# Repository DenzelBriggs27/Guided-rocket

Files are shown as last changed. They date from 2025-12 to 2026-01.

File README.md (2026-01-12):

# Guided-rocket
Project submission for an aerodynamically controlled rocket, with active stabilization achieved by aft fin control. The fins are controlled by a custom-made PCB based around the STM32f446RET6 MCU.
The goal of this rocket is to stabilize trajectory on the roll, pitch, and yaw, axes by deflecting the aft fins of the rocket, producing controlled side forces. This project will incorporate CFD, filters, and control systems to achieve this goal. 

This project is a step in my pursuit of a career in aerospace, granting me new knowledge in various areas that are difficult to gain hands-on experience with. This project could not be done without funding for the IC's.

CAD:

Screenshot 2025-12-11 at 12 46 26 PM

There were tons of updates and small changes made periodically, so I'm just going to show the finished product and do a general description of the process and mechanics.

Screenshot 2025-12-11 at 9 12 27 AM

This rocket is meant to fly on the 29mm G80t motor, which doesn't leave much room in the aft section for much, so I had to get creative with a servo linkage to the fins with a custom-made horn. The fins are connected to a connector which allows them to slot into a small circular bearing.

Screenshot 2025-12-11 at 12 00 54 PM
The servos are controlled by a pcb near the aft of the rocket

Screenshot 2025-12-11 at 12 01 56 PM
Screenshot 2025-12-11 at 12 03 56 PM

The parabay will hold the parachute and will separate after apogee, a raceway cable will travel along the side of the interior, containing the servos power and pwm wires.

Screenshot 2025-12-11 at 12 10 56 PM

Above the parabay is the lipo housing and avionics bay, the whole vehicle is powered by a 7.4v 2600mAh battery, supplying to the servos and flight computer. The avionics bay consists of my primary custom flight controller, a radio, and a microsd card breakout board for telemetry and flight data logging respectively.

Untitled design (3)

The ellipsoidal nose cone contains an esp32 s3 module with an ov2640 cam, this allows not only for footage, but for bluetooth and wifi capabilities, allowing setup processes such as fin actuation tests to be run from a phone.

PCB:

Screenshot 2025-12-12 at 4 37 38 PM
Screenshot 2025-12-12 at 4 47 43 PM

I designed a custom PCB for telemetry and guidance calculations, centered around a STM32f446RET6 MCU, and powered by a 7.4v LiPo battery. It has 3 IMUS: BMI088, H3LIS331DL, and a BNO085. These IMUs were chosen for their different G ranges, their data will be integrated into a Kalman filter, then used to calculate the correct fin deflection angle to correct the rocket's orientation. The board also has a SAM-M10q-00b GNSS receiver, a bmp390 altimeter, 2 pyro charges with continuity detection, 4 pwm outputs, an SPI output, and a UART output for telemetry with an XBee 900hp over the 900 mHz band. This radio link allows for commands to be sent by the ground center, for which I designed a slightly different PCB:

Screenshot 2025-12-11 at 1 38 38 PM
Screenshot 2025-12-11 at 1 39 33 PM
This PCB and a second xbee900hp allows for a radio datalink between the rocket and ground station, with a maximum range of ~28 miles. Over this radio datalink, telemetry (orientation, position, velocity, acceleration) and commands (fin tests, flight presets) will be sent.

Thanks for viewing my project!

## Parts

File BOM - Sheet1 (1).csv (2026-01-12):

Item | cost | total
all ics | 126.87 | 171.87
pcb order | 45

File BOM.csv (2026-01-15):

PCBWay Bom Quotation, Product No.:T-3P2W1045433A
Item # | *Designator | *Qty | *Mfg Part # | Vendor Part # | *Package/Footprint | *Unit Price(2 sets) | *Total | *Delivery Time | *Actual Purchase Mfg Part # | *PCBWay Note | Customer Reply | PCBWay Update
1 | C1, C10, C2, C3, C4, C5 | 6 | 100n |  | 0402 | $0.004 | $0.048 |  | CC0402KRX7R6BB104
2 | C11, C12 | 2 | 10p |  | 0402 | $0.007 | $0.028 |  | TCC0402COG100J500AT
3 | C13, C6 | 2 | 10u |  | 0603 | $0.048 | $0.192 |  | 0603X106M100NT
4 | C14 | 1 | 22u |  | 0805 | $0.162 | $0.324 |  | GRM21BR60J226ME39L
5 | C15, C16, C17, C18, C19, C21, C22, C25 | 8 | 0.1uf |  | 0402 | $0.003 | $0.048 |  | 0402B104K250NT
6 | C20, C26, C28 | 3 | 10uf |  | 0603 | $0.036 | $0.216 |  | 0603X106M100NT
7 | C23, C24 | 2 | 22pF |  | 0402 | $0.010 | $0.040 |  | CC0402JRNPO7BN220
8 | C27, C29, C38 | 3 | 22uF |  | 0805 | $0.065 | $0.390 |  | GRM21BR60J226ME39L
9 | C37 | 1 | 2.2uf |  | 0603 | $0.077 | $0.154 |  | TCC0603X5R225K100CT
10 | C41, C42 | 2 | 0.1u |  | 0402 | $0.010 | $0.040 |  | CC0402KRX7R6BB104
11 | C43 | 1 | 4.7u |  | 0402 | $0.065 | $0.130 |  | 0402X475M6R3NT
12 | C7 | 1 | 10n |  | 0402 | $0.016 | $0.032 |  | 0402B103K500NT
13 | C8, C9 | 2 | 1u |  | 0402 | $0.015 | $0.060 |  | 0402X105K100NT
14 | D1, D2 | 2 | RED |  | 0201 | $0.180 | $0.720 |  | XL-0201SURC | XL-0201SURC
15 | D3 | 1 | LTST-S270GKT |  | LTST_S270GKT | $0.116 | $0.232
16 | FB1 | 1 | FerriteBead |  | 0603 |  |  |  |  | Sunlord GZ1608D121TF
17 | J1 | 1 | 39357-0004 |  | 393570004 | $3.018 | $6.036
18 | J10, J5 | 2 | 1769 |  | 1769 | $1.173 | $4.692 |  |  | Adafruit Industries LLC
19 | J2 | 1 | Conn_01x04_Pin |  | PinHeader_1x04_P2.54mm_Vertical | $0.322 | $0.644 |  | B-2100S04P-A110 | B-2100S04P-A110
20 | J4, J7 | 2 | 1985849 |  | PHOENIX_1985849 | $1.454 | $5.816
21 | J6 | 1 | 1050171001 |  | MOLEX_1050171001 | $0.841 | $1.682
22 | J8, J9 | 2 | PRT-16766 |  | CONN_BM04B-SRSS-TB_SPK | $1.173 | $4.692 |  |  | PRT-16766
23 | L1, L2 | 2 | 22uH |  | 0603 | $0.066 | $0.264 |  | CMI160808J220KT | CMI160808J220KT brand FH
24 | L4 | 1 | 10uH |  | 0603 | $0.458 | $0.916 |  | SCL1608S100KSP | W SCL1608S100KSP brand Sunltech.
25 | LS1 | 1 | CMI-9653S-SMT |  | CUI_CMI-9653S-SMT | $5.019 | $10.038 |  | CMI-9653S-SMT-TR | CMI-9653S-SMT-TR
26 | R1, R10, R11 | 3 | 10k |  | 0402 | $0.004 | $0.024 |  | RC0402FR-0710KL
27 | R12, R5, R9 | 3 | 100 |  | 0402 | $0.004 | $0.024 |  | RC0402FR-07100RL
28 | R13, R14, R8 | 3 | 150 |  | 0402 | $0.004 | $0.024 |  | 0402WGF1500TCE
29 | R15 | 1 | 400 |  | 0805 | $0.833 | $1.666 |  | TR0805B400RP0525Z
30 | R16, R17 | 2 | 4.7k |  | 0402 | $0.005 | $0.020 |  | 0402WGF4701TCE
31 | R2, R7 | 2 | 1k |  | 0402 | $0.006 | $0.024 |  | RC0402FR-071KL
32 | R21, R4 | 2 | 470K |  | 0603 | $0.010 | $0.040 |  | RC0603FR-07470KL
33 | R22 | 1 | 150K |  | 0603 | $0.017 | $0.034 |  | 0603WAF1503T5E
34 | R3 | 1 | 150K |  | 0402 | $0.010 | $0.020 |  | 0402WGF1503TCE
35 | R6 | 1 | 100k |  | 0402 | $0.008 | $0.016 |  | 0402WGF1003TCE
36 | S1, S2, S3 | 3 | 450404015514 |  | 450404015514 | $1.460 | $8.760
37 | U1 | 1 | BNO085 |  | IC_BNO085 | $15.094 | $15.094 | 1
38 | U11, U12 | 2 | IRLML6344TRPBF | IRLML6344TRPBF | IRLML6344TRPBF | $1.001 | $4.004
39 | U13 | 1 | USBLC6-2SC6 |  | USBLC6_2SC6 | $0.722 | $1.444
40 | U14 | 1 | TPS2113ADRBR |  | TPS2113ADRBR | $1.065 | $2.130
41 | U15, U5 | 2 | TPS62160QDSGRQ1 |  | DSG0008A | $0.545 | $2.180
42 | U2 | 1 | BMI088 |  | BMI088 | $5.251 | $10.502
43 | U3 | 1 | TPS62177DQCT |  | TPS62177DQCT | $0.781 | $1.562
44 | U4 | 1 | AMS1117-3.3 |  | SOT-223-3_TabPin2 | $0.559 | $1.118 |  |  | AMS SOT-223
45 | U6 | 1 | BMP390L |  | XDCR_BMP390L | $4.495 | $8.990
46 | U7 | 1 | ABX00083 |  | ABX00083 | $19.300 | $19.300 | 1
47 | U8 | 1 | STM32F446RET6 |  | LQFP-64_10x10mm_P0.5mm | $4.830 | $9.660
48 | U9 | 1 | H3LIS331DL |  | H3LIS331DL | $21.368 | $21.368 | 1
49 | Y1 | 1 | 16MHz crystal |  | Crystal_SMD_3225-4Pin_3.2x2.5mm |  |  |  |  | X322516MMB4SI
50 | Y2 | 1 | NX3215SA-32.768K-STD-MUA-8 |  | XTAL_NX3215SA-32.768K-STD-MUA-8 | $0.367 | $0.734
 |  |  |  |  |  | Component Cost | $146.17
 |  |  |  |  |  | Shipping Cost | $43.50
 |  |  |  |  |  | PCB Cost
 |  |  |  |  |  | V0 Member 0% off | $0.00
 |  |  |  |  |  | All Total 2 Sets | $189.67

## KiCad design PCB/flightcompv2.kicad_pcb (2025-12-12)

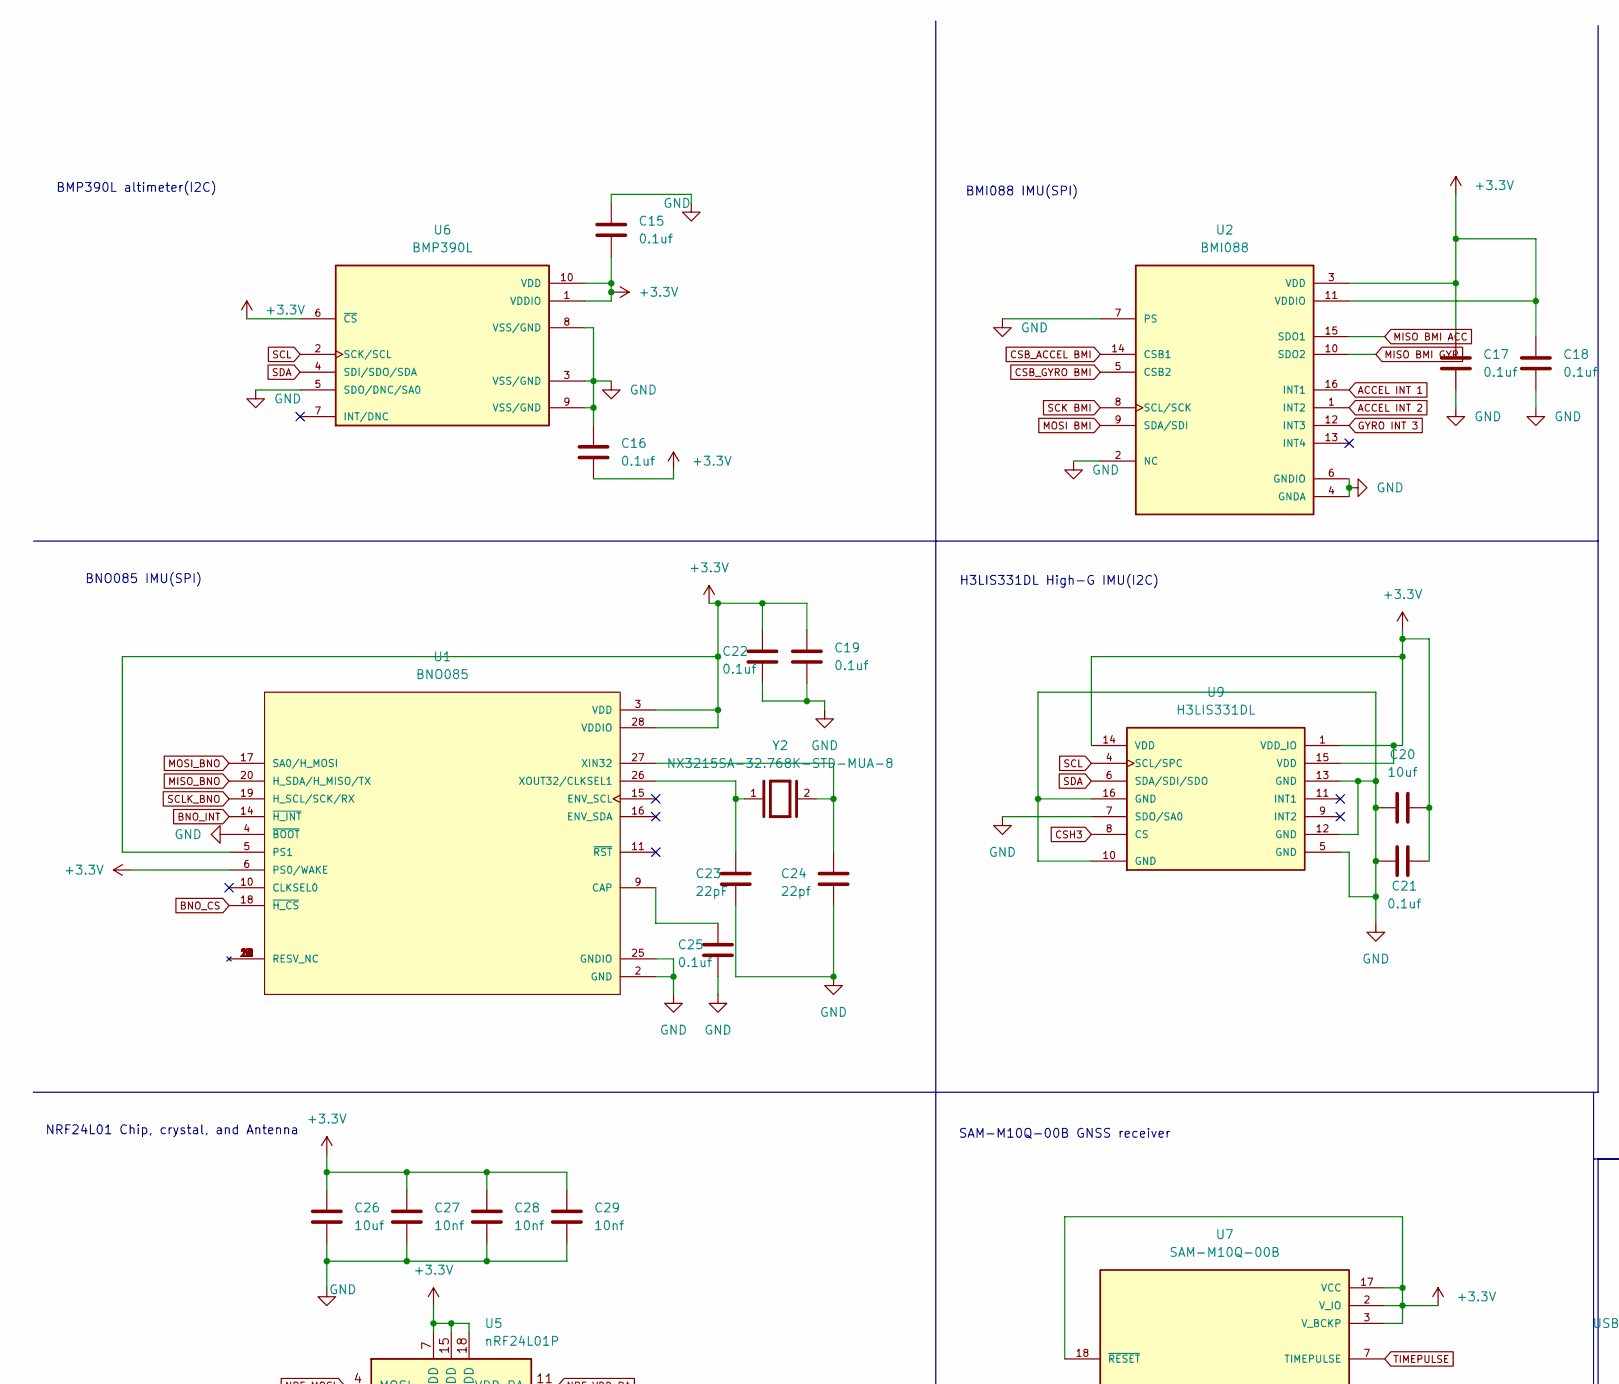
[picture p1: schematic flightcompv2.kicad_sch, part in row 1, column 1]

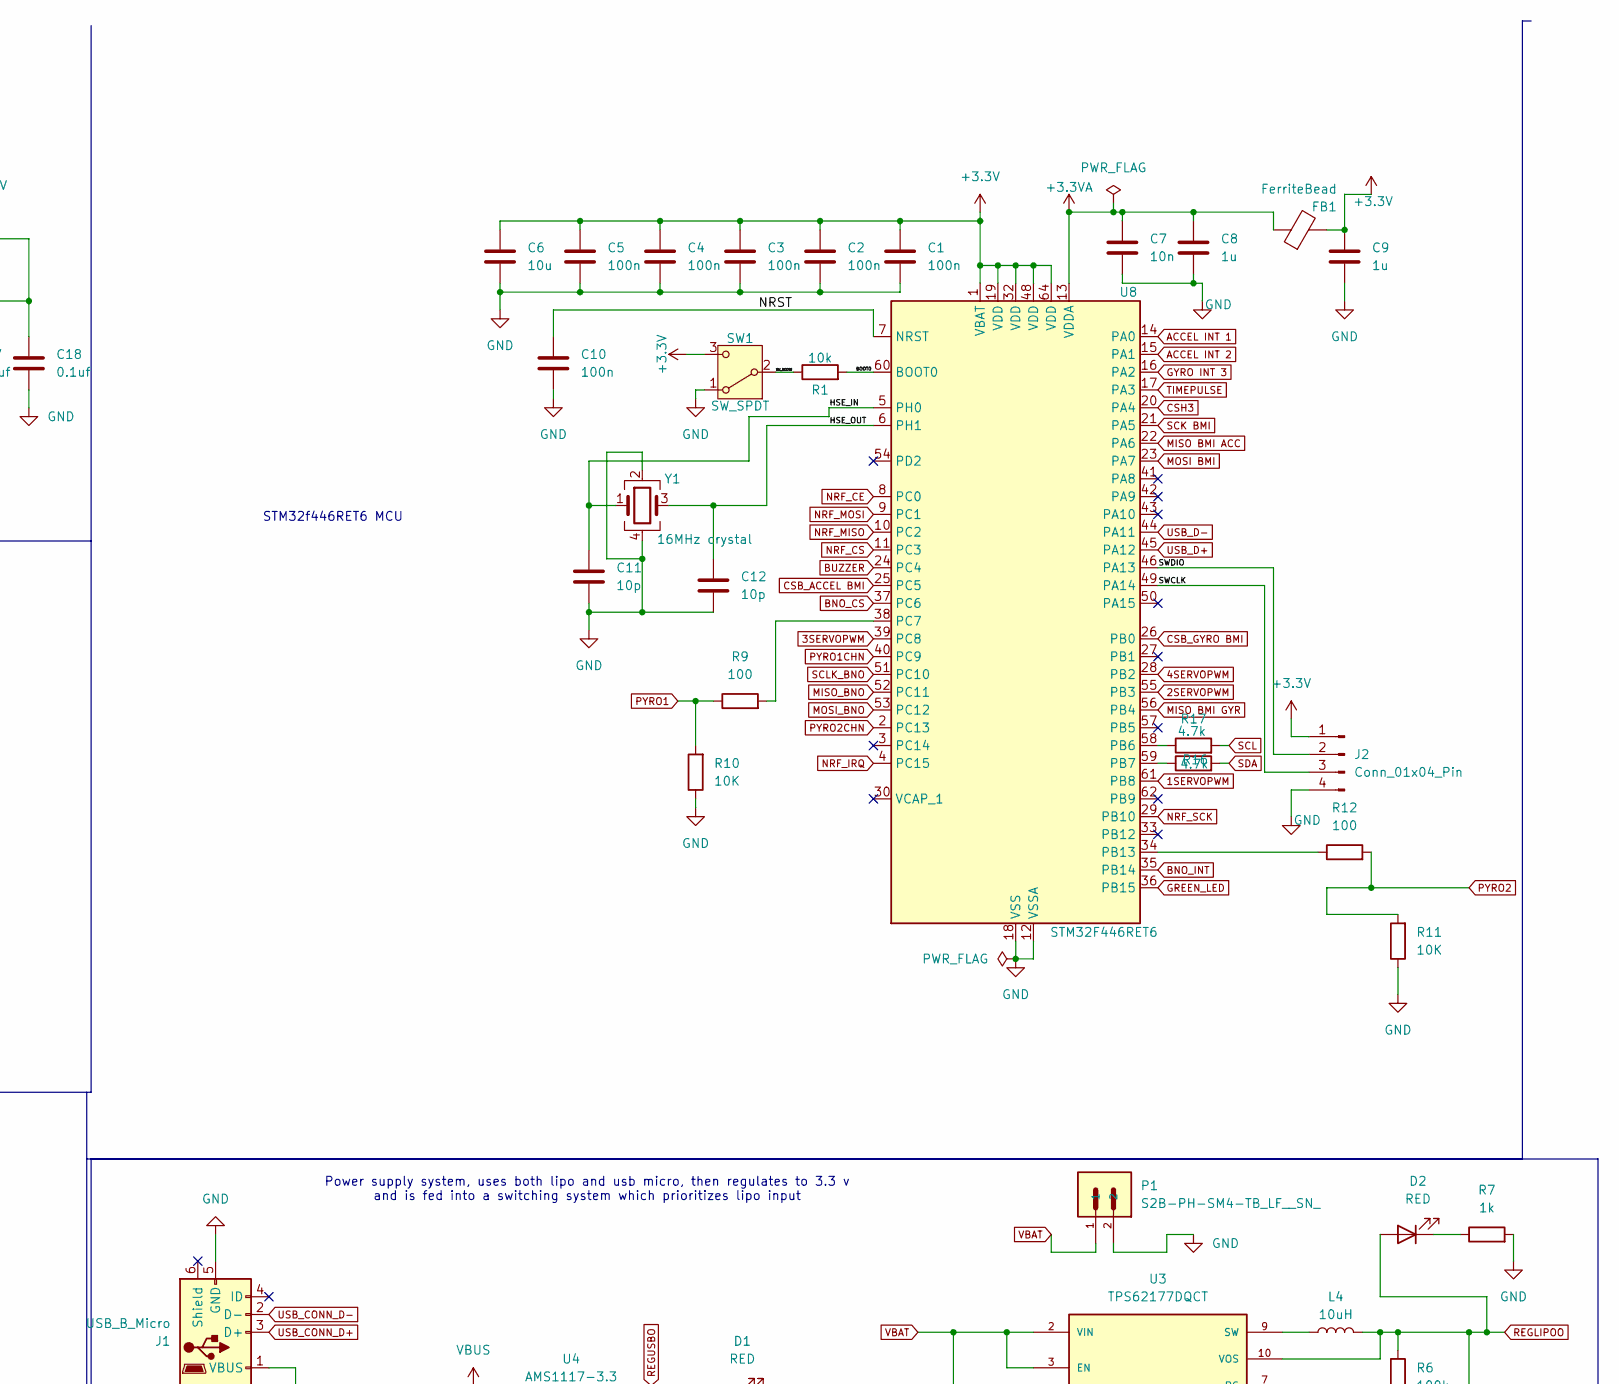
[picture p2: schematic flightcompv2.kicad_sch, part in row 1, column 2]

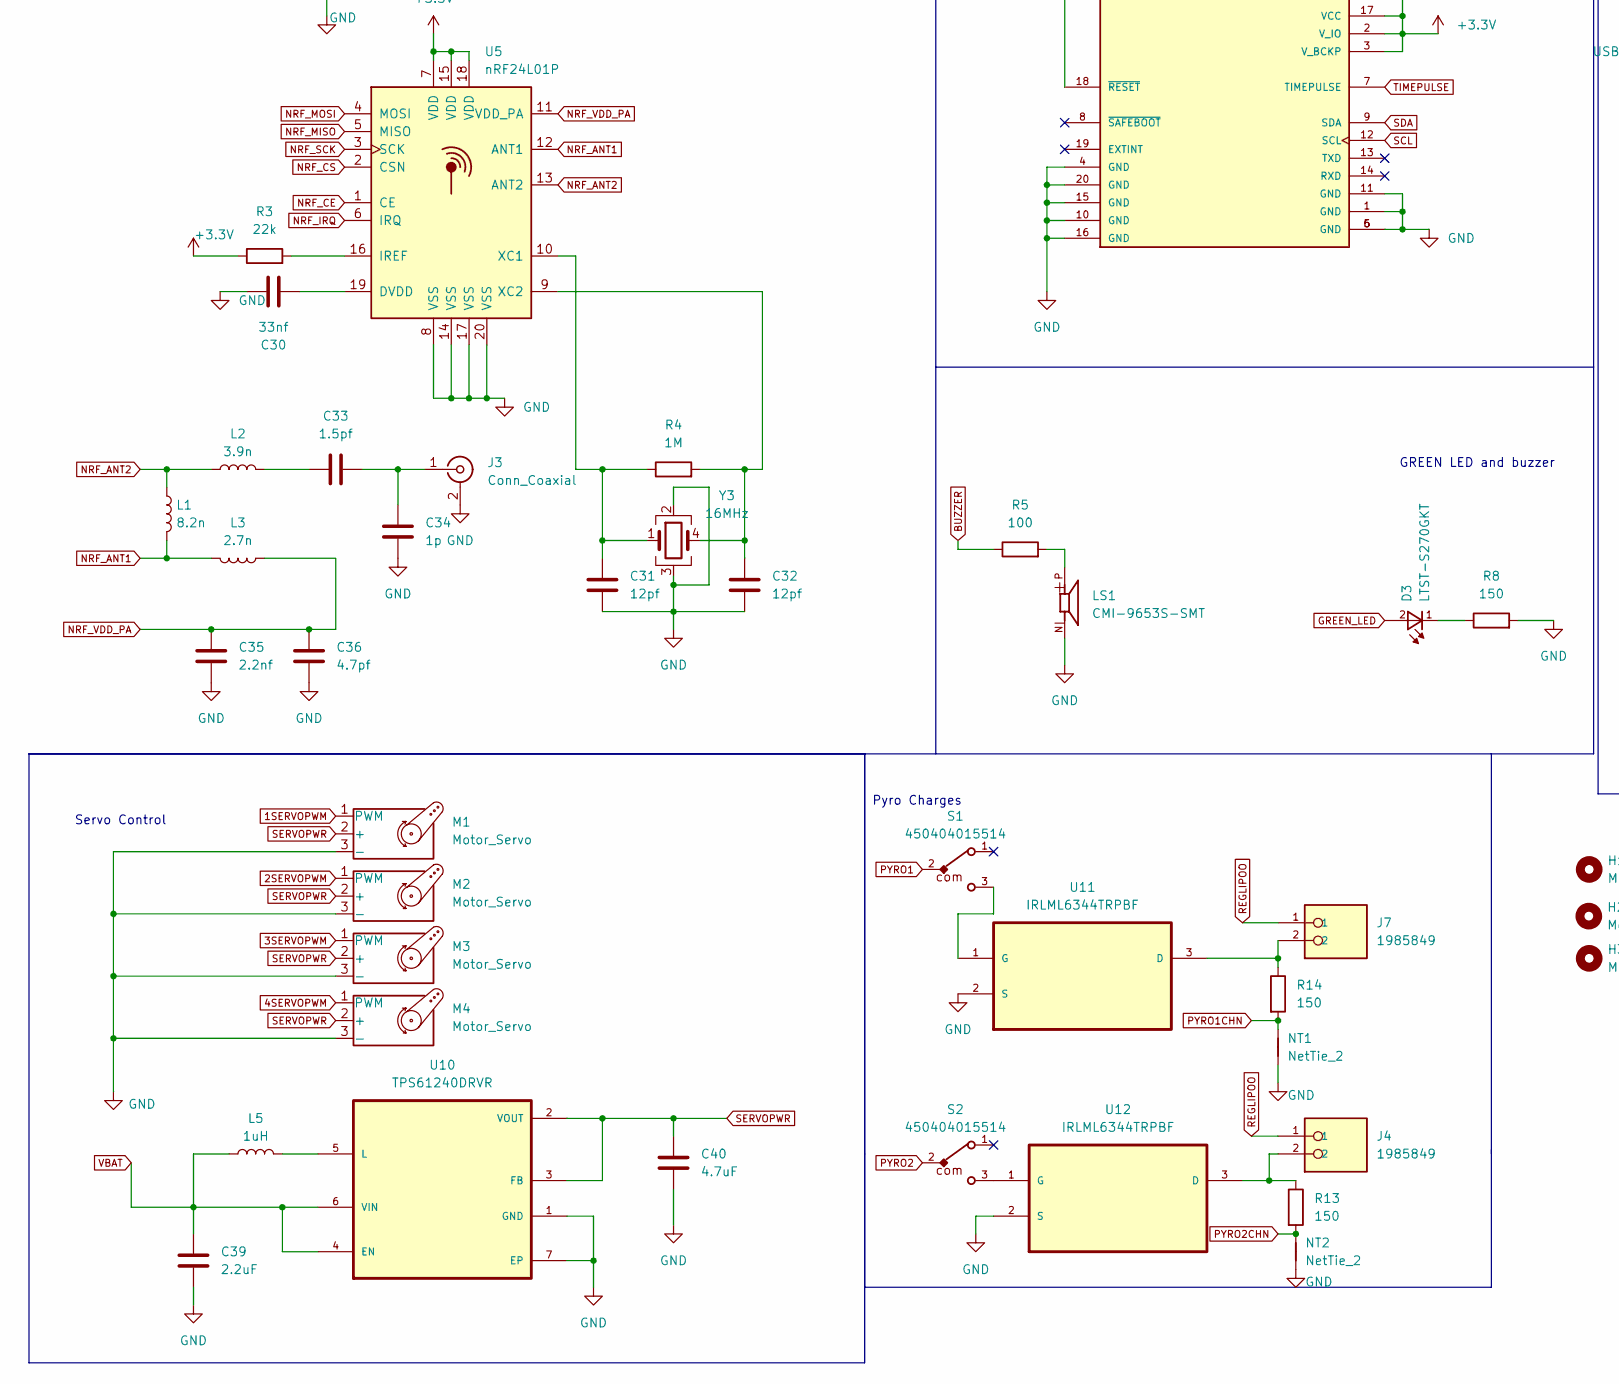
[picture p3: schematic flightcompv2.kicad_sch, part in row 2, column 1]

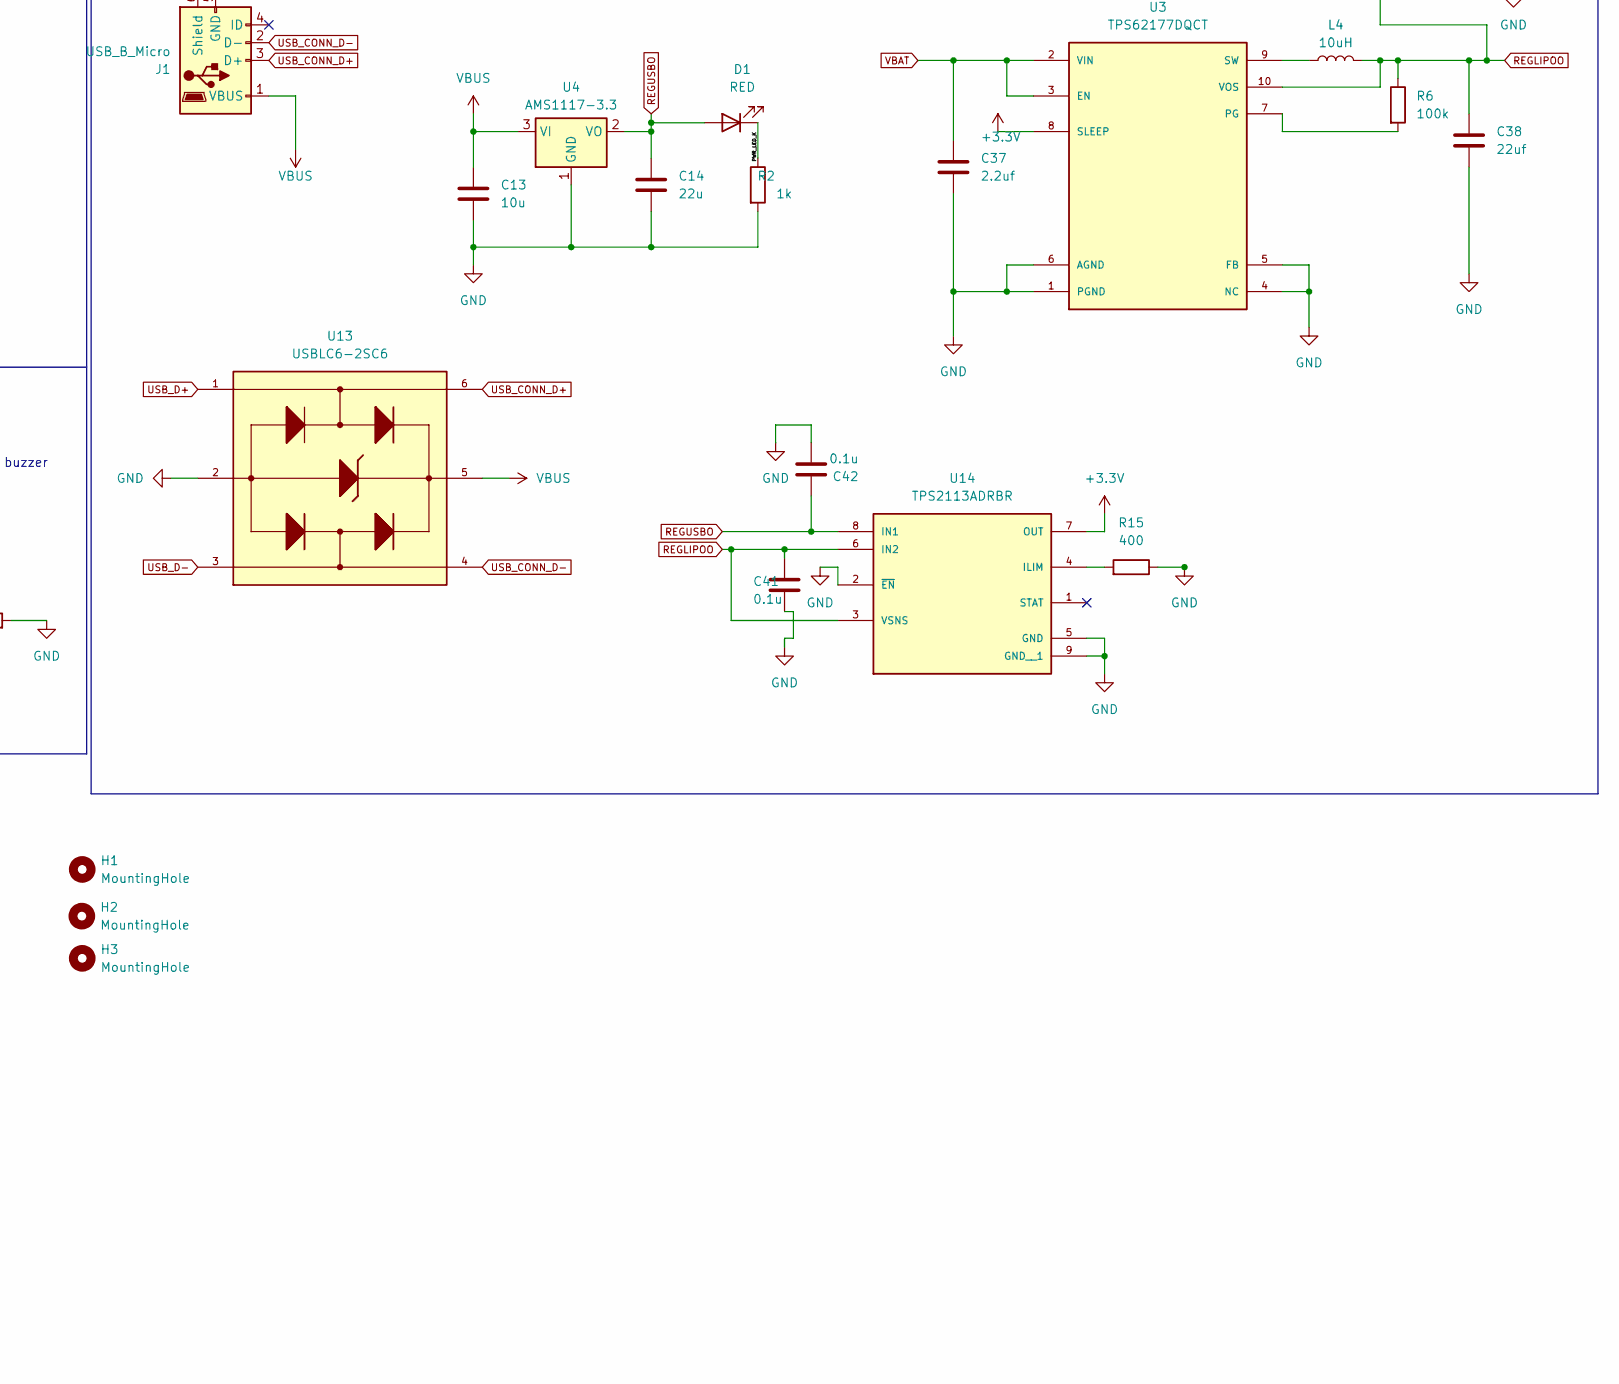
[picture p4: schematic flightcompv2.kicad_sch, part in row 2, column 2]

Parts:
C1, C2, C3, C4, C5, C10: 100n; C_0402_1005Metric
C6, C13: 10u; C_0603_1608Metric
C7: 10n; C_0402_1005Metric
C8, C9: 1u; C_0402_1005Metric
C11, C12: 10p; C_0402_1005Metric
C14: 22u; C_0805_2012Metric
C15, C16, C17, C18, C19, C21, C22, C25: 0.1uf; C_0402_1005Metric
C20, C26: 10uf; C_0603_1608Metric
C23: 22pF; C_0402_1005Metric
C24: 22pf; C_0402_1005Metric
C27, C28, C29: 10nf; C_0402_1005Metric
C30: 33nf; C_0402_1005Metric
C31, C32: 12pf; C_0402_1005Metric
C33: 1.5pf; C_0402_1005Metric
C34: 1p; C_0402_1005Metric
C35: 2.2nf; C_0402_1005Metric
C36: 4.7pf; C_0402_1005Metric
C37: 2.2uf; C_0603_1608Metric
C38: 22uf; C_0805_2012Metric
C39: 2.2uF; C_0603_1608Metric
C40: 4.7uF; C_0603_1608Metric
C41, C42: 0.1u; C_0402_1005Metric
D1, D2: RED; LED_0201_0603Metric
D3: LTST-S270GKT; LTST_S270GKT
FB1: FerriteBead; L_0603_1608Metric
H1, H2, H3: MountingHole; MountingHole_3.2mm_M3
J1: USB_B_Micro; USB_Micro-B_Wuerth_629105150521
J2: Conn_01x04_Pin; PinHeader_1x04_P2.54mm_Vertical
J3: Conn_Coaxial; SMA_Samtec_SMA-J-P-H-ST-EM1_EdgeMount
J4, J7: 1985849; PHOENIX_1985849; PARTREV 30.06.2022
L1: 8.2n; L_0402_1005Metric
L2: 3.9n; L_0402_1005Metric
L3: 2.7n; L_0402_1005Metric
L4: 10uH; L_0402_1005Metric
L5: 1uH; L_0402_1005Metric
LS1: CMI-9653S-SMT; CUI_CMI-9653S-SMT
M1, M2, M3, M4: Motor_Servo; PinHeader_1x03_P2.54mm_Vertical
NT1, NT2: NetTie_2
P1: S2B-PH-SM4-TB_LF__SN_; JST_S2B-PH-SM4-TB_LF__SN_
R1: 10k; R_0402_1005Metric
R2, R7: 1k; R_0402_1005Metric
R3: 22k; R_0402_1005Metric
R4: 1M; R_0402_1005Metric
R5, R9, R12: 100; R_0402_1005Metric
R6: 100k; R_0402_1005Metric
R8, R13, R14: 150; R_0402_1005Metric
R10, R11: 10K; R_0402_1005Metric
R15: 400; R_0402_1005Metric
R16, R17: 4.7k; R_0402_1005Metric
S1, S2: 450404015514
SW1: SW_SPDT; SW_Lever_1P2T_NKK_GW12LxH
U1: BNO085; IC_BNO085; PARTREV v1.17; DigiKey_Part_Number 1888-1006-2-ND
U2: BMI088
U3: TPS62177DQCT
U4: AMS1117-3.3; SOT-223-3_TabPin2
U5: nRF24L01P; QFN-20-1EP_4x4mm_P0.5mm_EP2.5x2.5mm
U6: BMP390L; XDCR_BMP390L; PARTREV 1.7
U7: SAM-M10Q-00B; XCVR_SAM-M10Q-00B; PARTREV R03; DigiKey_Part_Number 672-SAM-M10Q-00BTR-ND
U8: STM32F446RET6; LQFP-64_10x10mm_P0.5mm
U9: H3LIS331DL
U10: TPS61240DRVR
U11, U12: IRLML6344TRPBF; MPN IRLML6344TRPBF
U13: USBLC6-2SC6; USBLC6_2SC6
U14: TPS2113ADRBR; PARTREV C
Y1: 16MHz crystal; Crystal_SMD_3225-4Pin_3.2x2.5mm
Y2: NX3215SA-32.768K-STD-MUA-8; XTAL_NX3215SA-32.768K-STD-MUA-8; PARTREV 2003D_NX3215SA_e
Y3: 16MHz; Crystal_SMD_3225-4Pin_3.2x2.5mm

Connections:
1SERVOPWM: M1.1 (PWM), U8.61 (PB8)
2SERVOPWM: M2.1 (PWM), U8.55 (PB3)
3SERVOPWM: M3.1 (PWM), U8.39 (PC8)
4SERVOPWM: M4.1 (PWM), U8.28 (PB2)
+3.3V: C1.1, C2.1, C3.1, C4.1, C5.1, C6.1, C9.1, C15.2, C16.2, C17.2, C18.2, C19.1, C20.2, C21.2, C22.1, C26.1, C27.1, C28.1, C29.1, FB1.2, J2.1, R3.1, SW1.3 (C), U1.3 (VDD), U1.5 (PS1), U1.6 (PS0/WAKE), U1.28 (VDDIO), U2.3 (VDD), U2.11 (VDDIO), U3.8 (SLEEP), U5.7 (VDD), U5.15 (VDD), U5.18 (VDD), U6.1 (VDDIO), U6.6 (~CS), U6.10 (VDD), U7.2 (V_IO), U7.3 (V_BCKP), U7.17 (VCC), U7.18 (~RESET), U8.1 (VBAT), U8.19 (VDD), U8.32 (VDD), U8.48 (VDD), U8.64 (VDD), U9.1 (VDD_IO), U9.14 (VDD), U9.15 (VDD), U14.7 (OUT)
+3.3VA: C7.1, C8.1, FB1.1, U8.13 (VDDA)
/BOOT0: R1.2, U8.60 (BOOT0)
/HSE_IN: C11.1, U8.5 (PH0), Y1.1
/HSE_OUT: C12.1, U8.6 (PH1), Y1.3
/NRST: C10.1, U8.7 (NRST)
/PWR_LED_K: D1.1 (K), R2.1
/SWCLK: J2.3, U8.49 (PA14)
/SWDIO: J2.2, U8.46 (PA13)
/SW_BOOT0: R1.1, SW1.2 (B)
ACCEL INT 1: U2.16 (INT1), U8.14 (PA0)
ACCEL INT 2: U2.1 (INT2), U8.15 (PA1)
BNO_CS: U1.18 (~H_CS), U8.37 (PC6)
BNO_INT: U1.14 (~H_INT), U8.35 (PB14)
BUZZER: R5.1, U8.24 (PC4)
CSB_ACCEL BMI: U2.14 (CSB1), U8.25 (PC5)
CSB_GYRO BMI: U2.5 (CSB2), U8.26 (PB0)
CSH3: U8.20 (PA4), U9.8 (CS)
GND: C1.2, C2.2, C3.2, C4.2, C5.2, C6.2, C7.2, C8.2, C9.2, C10.2, C11.2, C12.2, C13.2, C14.2, C15.1, C16.1, C17.1, C18.1, C19.2, C20.1, C21.1, C22.2, C23.2, C24.2, C25.2, C26.2, C27.2, C28.2, C29.2, C30.2, C31.2, C32.2, C34.1, C35.1, C36.1, C37.2, C38.2, C39.2, C40.2, C41.2, C42.2, J1.5 (GND), J2.4, J3.2 (Ext), LS1.N, M1.3 (-), M2.3 (-), M3.3 (-), M4.3 (-), NT1.1, NT2.1, P1.2, R2.2, R7.2, R8.2, R10.1, R11.1, R15.1, SW1.1 (A), U1.2 (GND), U1.4 (~BOOT), U1.25 (GNDIO), U2.2 (NC), U2.4 (GNDA), U2.6 (GNDIO), U2.7 (PS), U3.1 (PGND), U3.4 (NC), U3.5 (FB), U3.6 (AGND), U4.1 (GND), U5.8 (VSS), U5.14 (VSS), U5.17 (VSS), U5.20 (VSS), U6.3 (VSS/GND), U6.5 (SDO/DNC/SA0), U6.8 (VSS/GND), U6.9 (VSS/GND), U7.1 (GND), U7.4 (GND), U7.5 (GND), U7.6 (GND), U7.10 (GND), U7.11 (GND), U7.15 (GND), U7.16 (GND), U7.20 (GND), U8.12 (VSSA), U8.18 (VSS), U8.31 (VSS), U8.47 (VSS), U8.63 (VSS), U9.5 (GND), U9.7 (SDO/SA0), U9.10 (GND), U9.12 (GND), U9.13 (GND), U9.16 (GND), U10.1 (GND), U10.7 (EP), U11.2 (S), U12.2 (S), U13.2, U14.2 (~EN), U14.5 (GND), U14.9 (GND__1), Y1.2, Y1.4, Y3.2, Y3.3
GREEN_LED: D3.2, U8.36 (PB15)
GYRO INT 3: U2.12 (INT3), U8.16 (PA2)
MISO BMI ACC: U2.15 (SDO1), U8.22 (PA6)
MISO BMI GYR: U2.10 (SDO2), U8.56 (PB4)
MISO_BNO: U1.20 (H_SDA/H_MISO/TX), U8.52 (PC11)
MOSI BMI: U2.9 (SDA/SDI), U8.23 (PA7)
MOSI_BNO: U1.17 (SA0/H_MOSI), U8.53 (PC12)
NRF_ANT1: L1.2, L3.2, U5.12 (ANT1)
NRF_ANT2: L1.1, L2.1, U5.13 (ANT2)
NRF_CE: U5.1 (CE), U8.8 (PC0)
NRF_CS: U5.2 (CSN), U8.11 (PC3)
NRF_IRQ: U5.6 (IRQ), U8.4 (PC15)
NRF_MISO: U5.5 (MISO), U8.10 (PC2)
NRF_MOSI: U5.4 (MOSI), U8.9 (PC1)
NRF_SCK: U5.3 (SCK), U8.29 (PB10)
NRF_VDD_PA: C35.2, C36.2, L3.1, U5.11 (VDD_PA)
unnamed: C33.1, L2.2
unnamed: D2.1 (K), R7.1
unnamed: D3.1, R8.1
unnamed: C33.2, C34.2, J3.1 (In)
unnamed: LS1.P, R5.2
unnamed: C25.1, U1.9 (CAP)
unnamed: C24.1, U1.27 (XIN32), Y2.2
unnamed: C23.1, U1.26 (XOUT32/CLKSEL1), Y2.1
unnamed: R6.2, U3.7 (PG)
unnamed: L4.1, U3.9 (SW)
unnamed: C30.1, U5.19 (DVDD)
unnamed: R3.2, U5.16 (IREF)
unnamed: C31.1, R4.1, U5.10 (XC1), Y3.1
unnamed: C32.1, R4.2, U5.9 (XC2), Y3.4
unnamed: R16.1, U8.58 (PB6)
unnamed: R17.1, U8.59 (PB7)
unnamed: R12.1, U8.34 (PB13)
unnamed: R9.2, U8.38 (PC7)
unnamed: L5.2, U10.5 (L)
unnamed: J7.2, R14.1, U11.3 (D)
unnamed: S1.3, U11.1 (G)
unnamed: J4.2, R13.1, U12.3 (D)
unnamed: S2.3, U12.1 (G)
unnamed: R15.2, U14.4 (ILIM)
PYRO1: R9.1, R10.2, S1.2
PYRO1CHN: NT1.2, R14.2, U8.40 (PC9)
PYRO2: R11.2, R12.2, S2.2
PYRO2CHN: NT2.2, R13.2, U8.2 (PC13)
REGLIPOO: C38.1, C41.1, D2.2 (A), J4.1, J7.1, L4.2, R6.1, U3.10 (VOS), U14.3 (VSNS), U14.6 (IN2)
REGUSBO: C14.1, C42.1, D1.2 (A), U4.2 (VO), U14.8 (IN1)
SCK BMI: U2.8 (SCL/SCK), U8.21 (PA5)
SCL: R16.2, U6.2 (SCK/SCL), U7.12 (SCL), U9.4 (SCL/SPC)
SCLK_BNO: U1.19 (H_SCL/SCK/RX), U8.51 (PC10)
SDA: R17.2, U6.4 (SDI/SDO/SDA), U7.9 (SDA), U9.6 (SDA/SDI/SDO)
SERVOPWR: C40.1, M1.2 (+), M2.2 (+), M3.2 (+), M4.2 (+), U10.2 (VOUT), U10.3 (FB)
TIMEPULSE: U7.7 (TIMEPULSE), U8.17 (PA3)
USB_CONN_D+: J1.3 (D+), U13.6
USB_CONN_D-: J1.2 (D-), U13.4
USB_D+: U8.45 (PA12), U13.1
USB_D-: U8.44 (PA11), U13.3
VBAT: C37.1, C39.1, L5.1, P1.1, U3.2 (VIN), U3.3 (EN), U10.4 (EN), U10.6 (VIN)
VBUS: C13.1, J1.1 (VBUS), U4.3 (VI), U13.5

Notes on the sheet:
Pyro Charges
BMP390L altimeter(I2C)
BMI088 IMU(SPI)
NRF24L01 Chip, crystal, and Antenna
GREEN LED and buzzer
H3LIS331DL High-G IMU(I2C)
STM32f446RET6 MCU
Power supply system, uses both lipo and usb micro, then regulates to 3.3 v and is fed into a switching system which prioritizes lipo input
BNO085 IMU(SPI)
Servo Control
SAM-M10Q-00B GNSS receiver

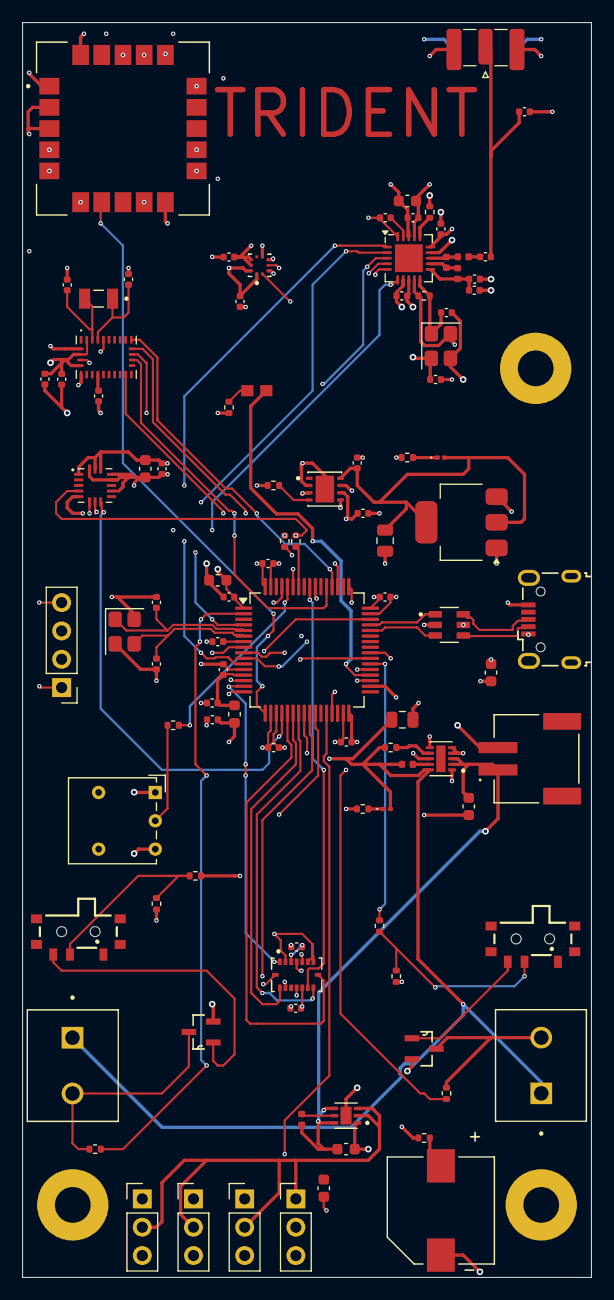
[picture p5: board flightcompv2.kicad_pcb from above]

Board: 6 copper layers, 51.0 x 112.5 mm, 102 parts (0 on the bottom side), 81 nets.

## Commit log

2025-12-26 Add files via upload
    Uploaded BOM
    [BOM - Sheet1.csv]
2026-01-12 Delete BOM - Sheet1.csv
    changing bom
    [BOM - Sheet1.csv]
2026-01-14 Update and rename T-3P2W1045433A-2sets-bom(2025-12-20) - Sheet1 (1).csv to BOM(components).csv
    [BOM(components).csv]
2026-01-14 Update and rename BOM - Sheet1 (1).csv to BOM(total).csv
    [BOM(total).csv]
2026-01-15 Update and rename T-3P2W1045433A-2sets-bom(2025-12-20) - Sheet1 (2).csv to BOM.csv
    [BOM.csv]
